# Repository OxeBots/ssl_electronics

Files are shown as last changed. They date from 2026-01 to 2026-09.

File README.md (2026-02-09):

# SSL Electronics - Oxebots

Electronics design for the RoboCup Soccer Small-Size League (SSL).

## System Architecture

*   **Main Board:** ESP32-based controller board.
*   **Power Board:** Power distribution and battery protection.
*   **Kicker Board:** Board that drives the solenoid through a capacitor bank charged up to 200V.

## Repository Structure

*   `/pcbs`: KiCad boards project files.
*   `/Libraries`: Custom symbols, footprints, and 3D models.
*   `/exported`: STEP and 3D exports.
*   `/datasheets`: Component documentation.

## Core Components

*   **Toolchain:** KiCad 9.0+
*   **MCU:** ESP32 38-pin
*   **RF:** NRF24L01+
*   **Sensors:** GY-85 (IMU), AS5600 (motor encoder), VL53L5X (ToF sensor)
*   **Motors:** BL48250 motor with driver board (for 24V).
*   **Solenoid:** 25X50TL (for 24V)

## Configuration

To resolve library dependencies in KiCad, you must configure the `OXEBOTS_SSL_LIB_DIR` path variable:

1.  Open KiCad.
2.  Go to **Preferences** > **Configure Paths...**
3.  Add a new entry (+ symbol):
    *   **Name:** `OXEBOTS_SSL_LIB_DIR`
    *   **Path:** Path to the `Libraries` folder in your local machine.

This ensures all schematic symbols, footprints, and 3D models are correctly linked.

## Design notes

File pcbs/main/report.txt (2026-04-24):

Footprints que foram alterados M3 de 'Oxebots:NRF24L01' para 'Oxebots:NRF24L01': : OK
Footprints que foram alterados M4 de 'Oxebots:NRF24L01' para 'Oxebots:NRF24L01': : OK
Footprints que foram alterados M2 de 'Oxebots:NRF24L01' para 'Oxebots:NRF24L01': : OK
Footprints que foram alterados M1 de 'Oxebots:NRF24L01' para 'Oxebots:NRF24L01': : OK
Footprints que foram alterados PCB2 de 'Oxebots:NRF24L01' para 'Oxebots:NRF24L01': : OK

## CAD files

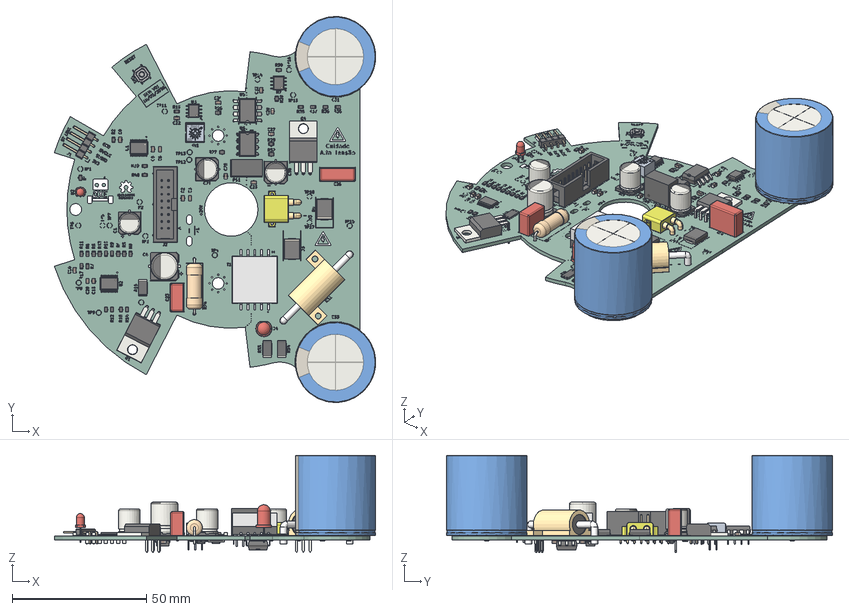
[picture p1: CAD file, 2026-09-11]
exported/kicker_board.step
119.9 x 144.0 x 36.3 mm
PinHeader_1x04_P254mm_Horizontal
CP_Elec_10x125
CP_Elec_8x10 x 3
R_0805_2012Metric x 34
C_Rect_L103mm_W50mm_P750mm_MKS4
TDK_DCT15EFD-U44S003 v1
TSSOP-20_4.4x6.5mm_P0.65mm x 2
C_0805_2012Metric x 25
TO-220-3_Horizontal_TabDown x 2
LED_D5.0mm
3362A_TAA
IDC_Header_2x08_P254mm_Vertical
DIP-8_W10.16mm
resistor_rx24_10w v1
R_Axial_DIN0617_L170mm_D60mm_P2032mm_Horizontal
R_2512_6332Metric x 4
C_Rect_L130mm_W50mm_P1000mm_FKS3_FKP3_MKS4
DIP-8_W7.62mm
LED_D3.0mm
CP_Radial_D300mm_P1000mm_SnapIn x 2
D_SMC x 2
SOIC-8_3.9x4.9mm_P1.27mm x 2
XT30PW-M
SW_SPST_SKQG_WithStem
MORNSUN BxxxxS-1WR3 v2
SOT-23 x 2
D_SMB
DIP_6_W889mm_SMDSocket
Kicker_LT3751_OxeBots_silkscreen x 2
Kicker_LT3751_OxeBots_PCB

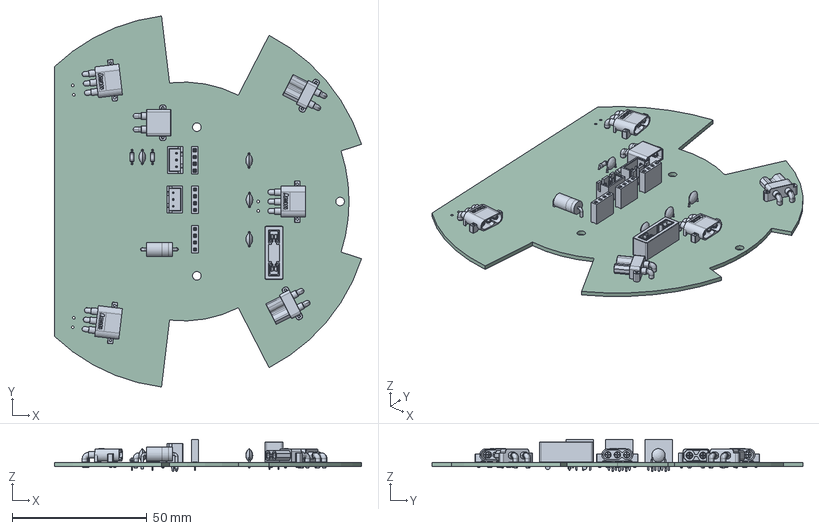
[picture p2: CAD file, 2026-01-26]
exported/power_board.step
114.0 x 137.6 x 11.9 mm
PinSocket_1x04_P2.54mm_Vertical x 3
C_Disc_D5.0mm_W2.5mm_P5.00mm x 4
power_board 1.3.1 x 3
power_board 1.3.2 x 3
power_board 1.3.3 x 3
power_board 1.3.4 x 3
power_board 1.3.5 x 3
D_DO-201_P12.70mm_Horizontal
JST_XH_B3B-XH-A_1x03_P2.50mm_Vertical x 2
XT30PW-M
R_Axial_DIN0204_L3.6mm_D1.6mm_P5.08mm_Horizontal x 2
XT30PW-F x 2
power_board_PCB

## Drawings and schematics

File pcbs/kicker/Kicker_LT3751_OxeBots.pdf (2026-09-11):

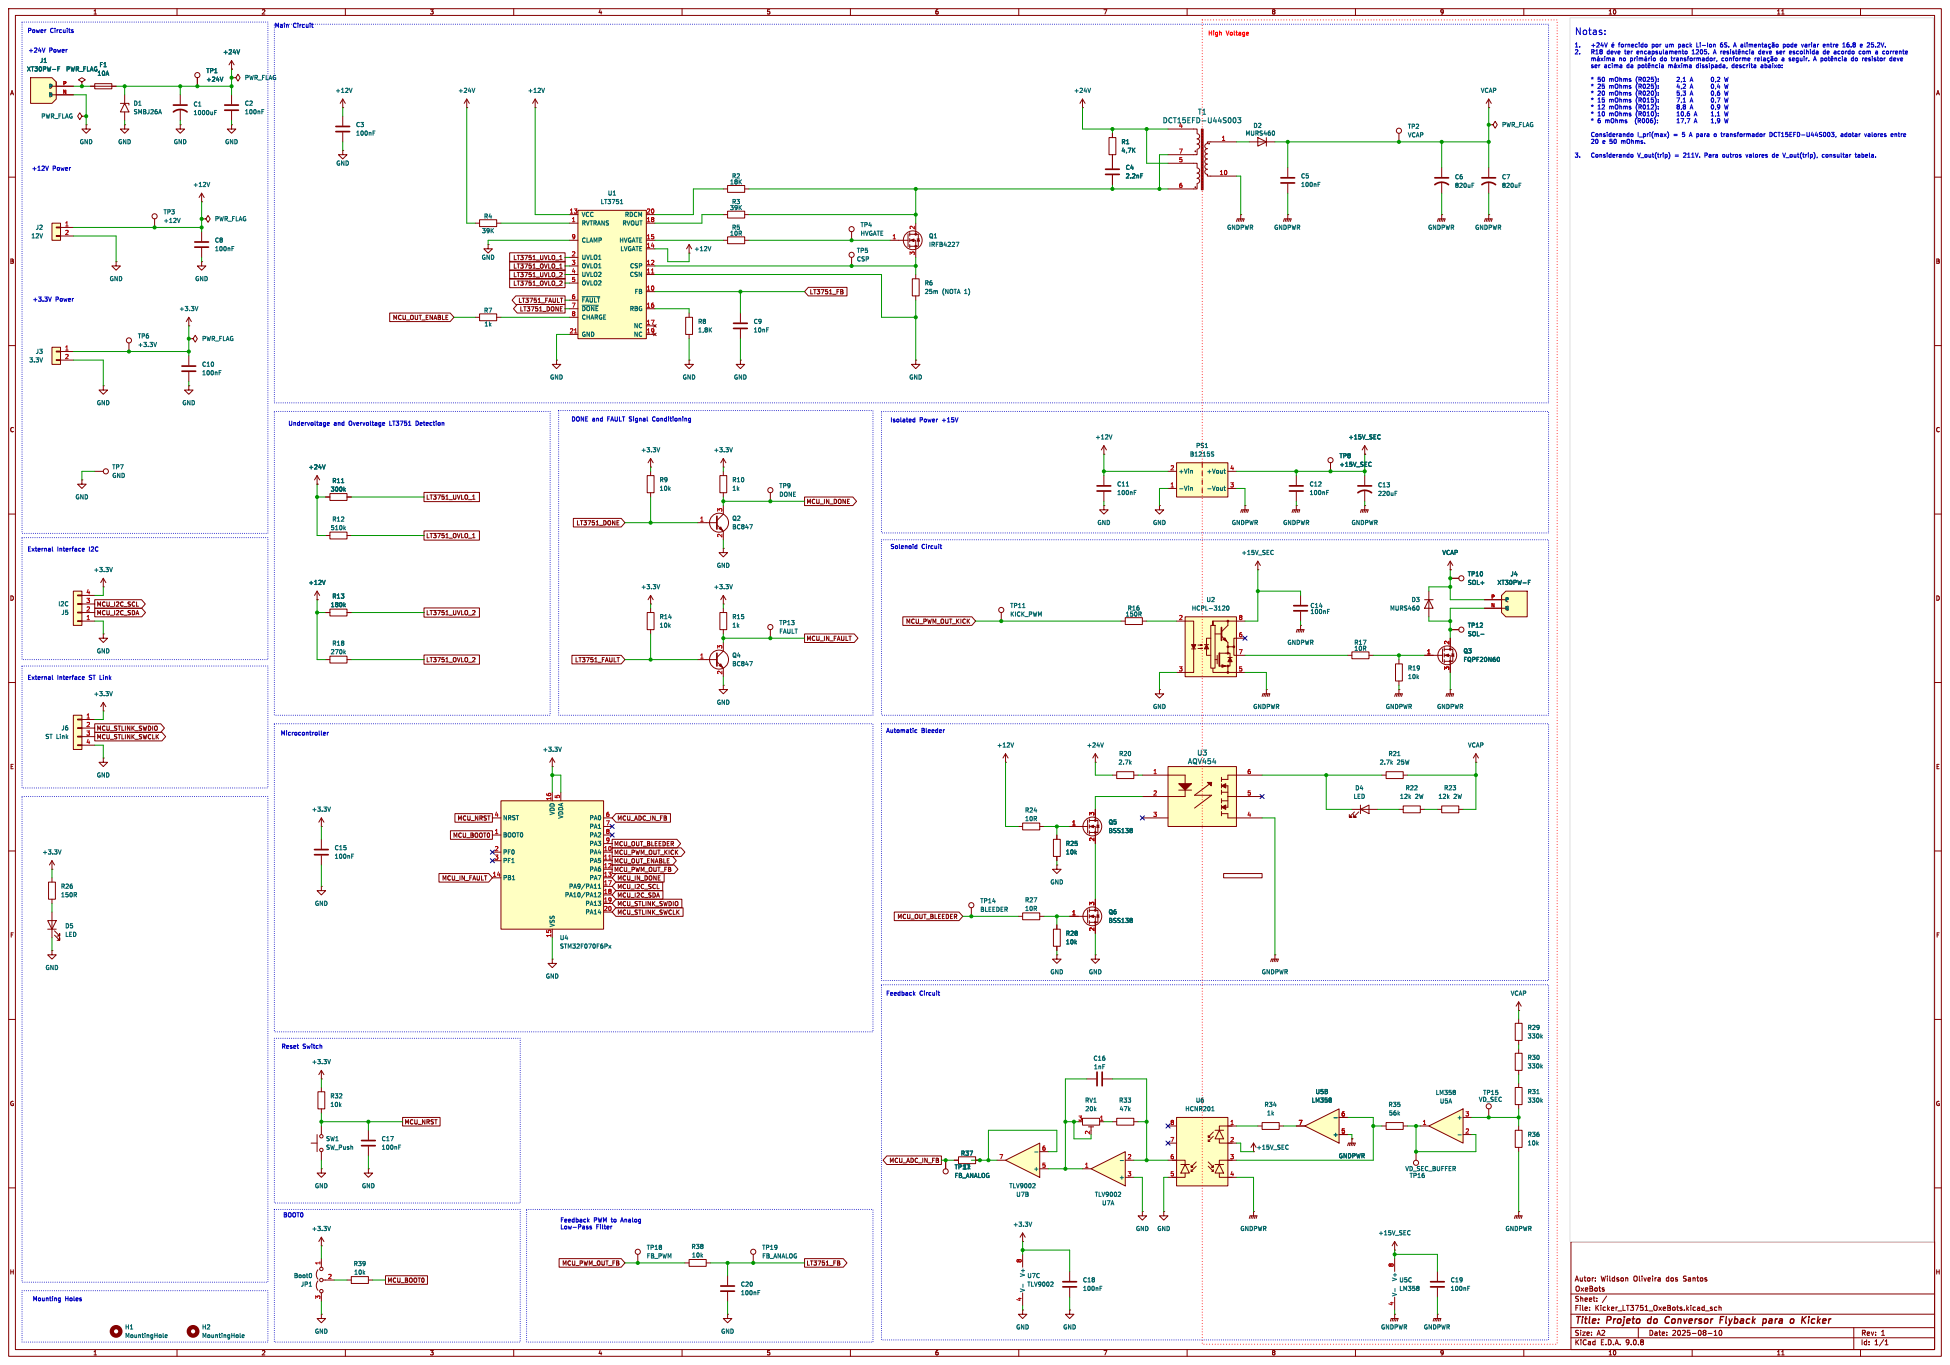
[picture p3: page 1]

LVGATE 14 CSP 12 CSN 11 FB 10 RBG 16 NC 17 NC 19 U1

Feedback PWM to Analog

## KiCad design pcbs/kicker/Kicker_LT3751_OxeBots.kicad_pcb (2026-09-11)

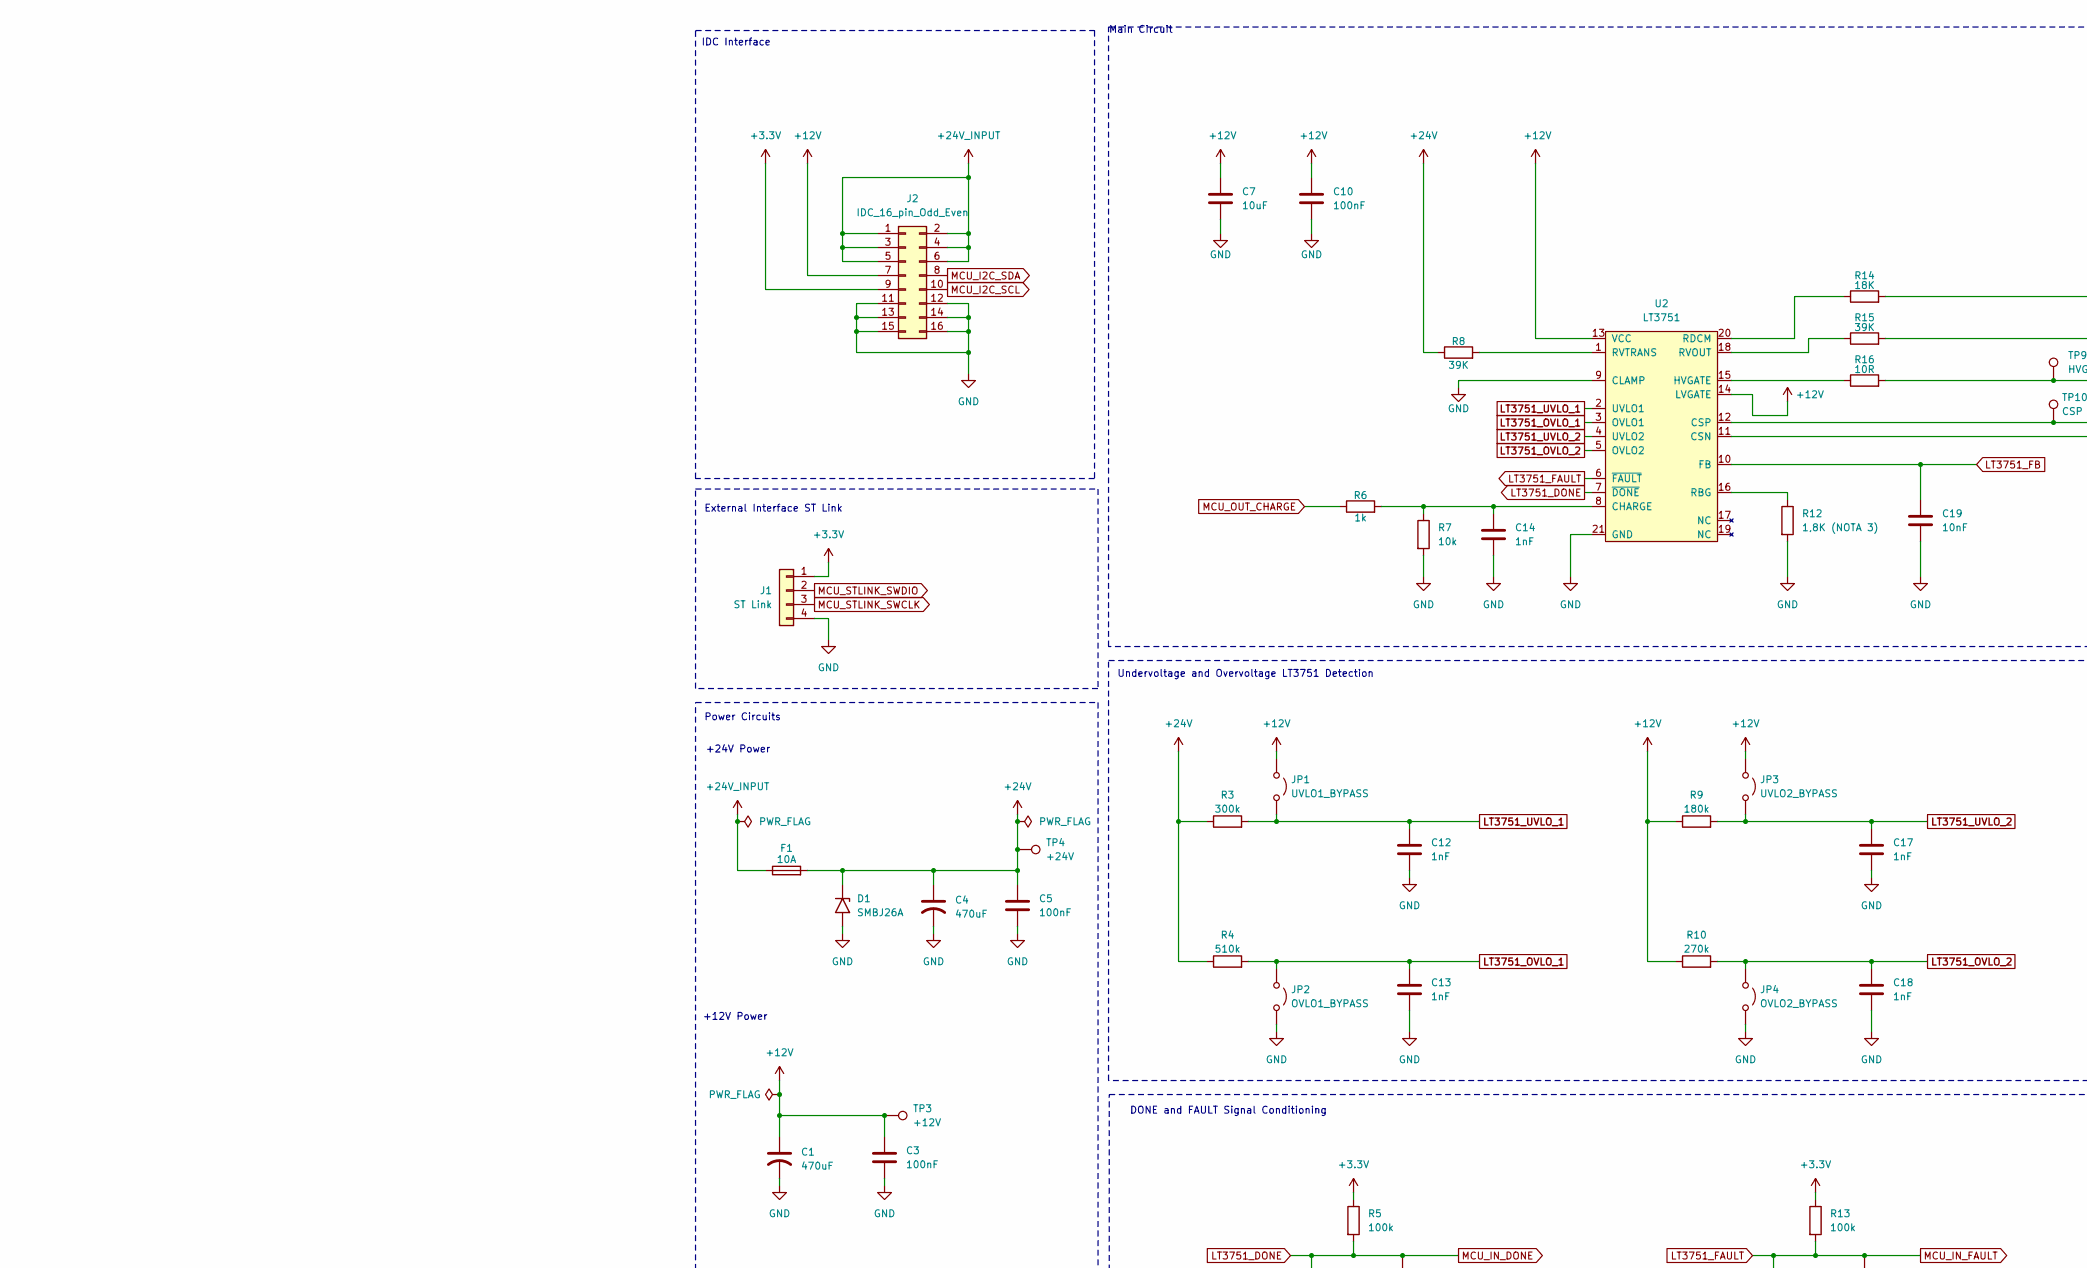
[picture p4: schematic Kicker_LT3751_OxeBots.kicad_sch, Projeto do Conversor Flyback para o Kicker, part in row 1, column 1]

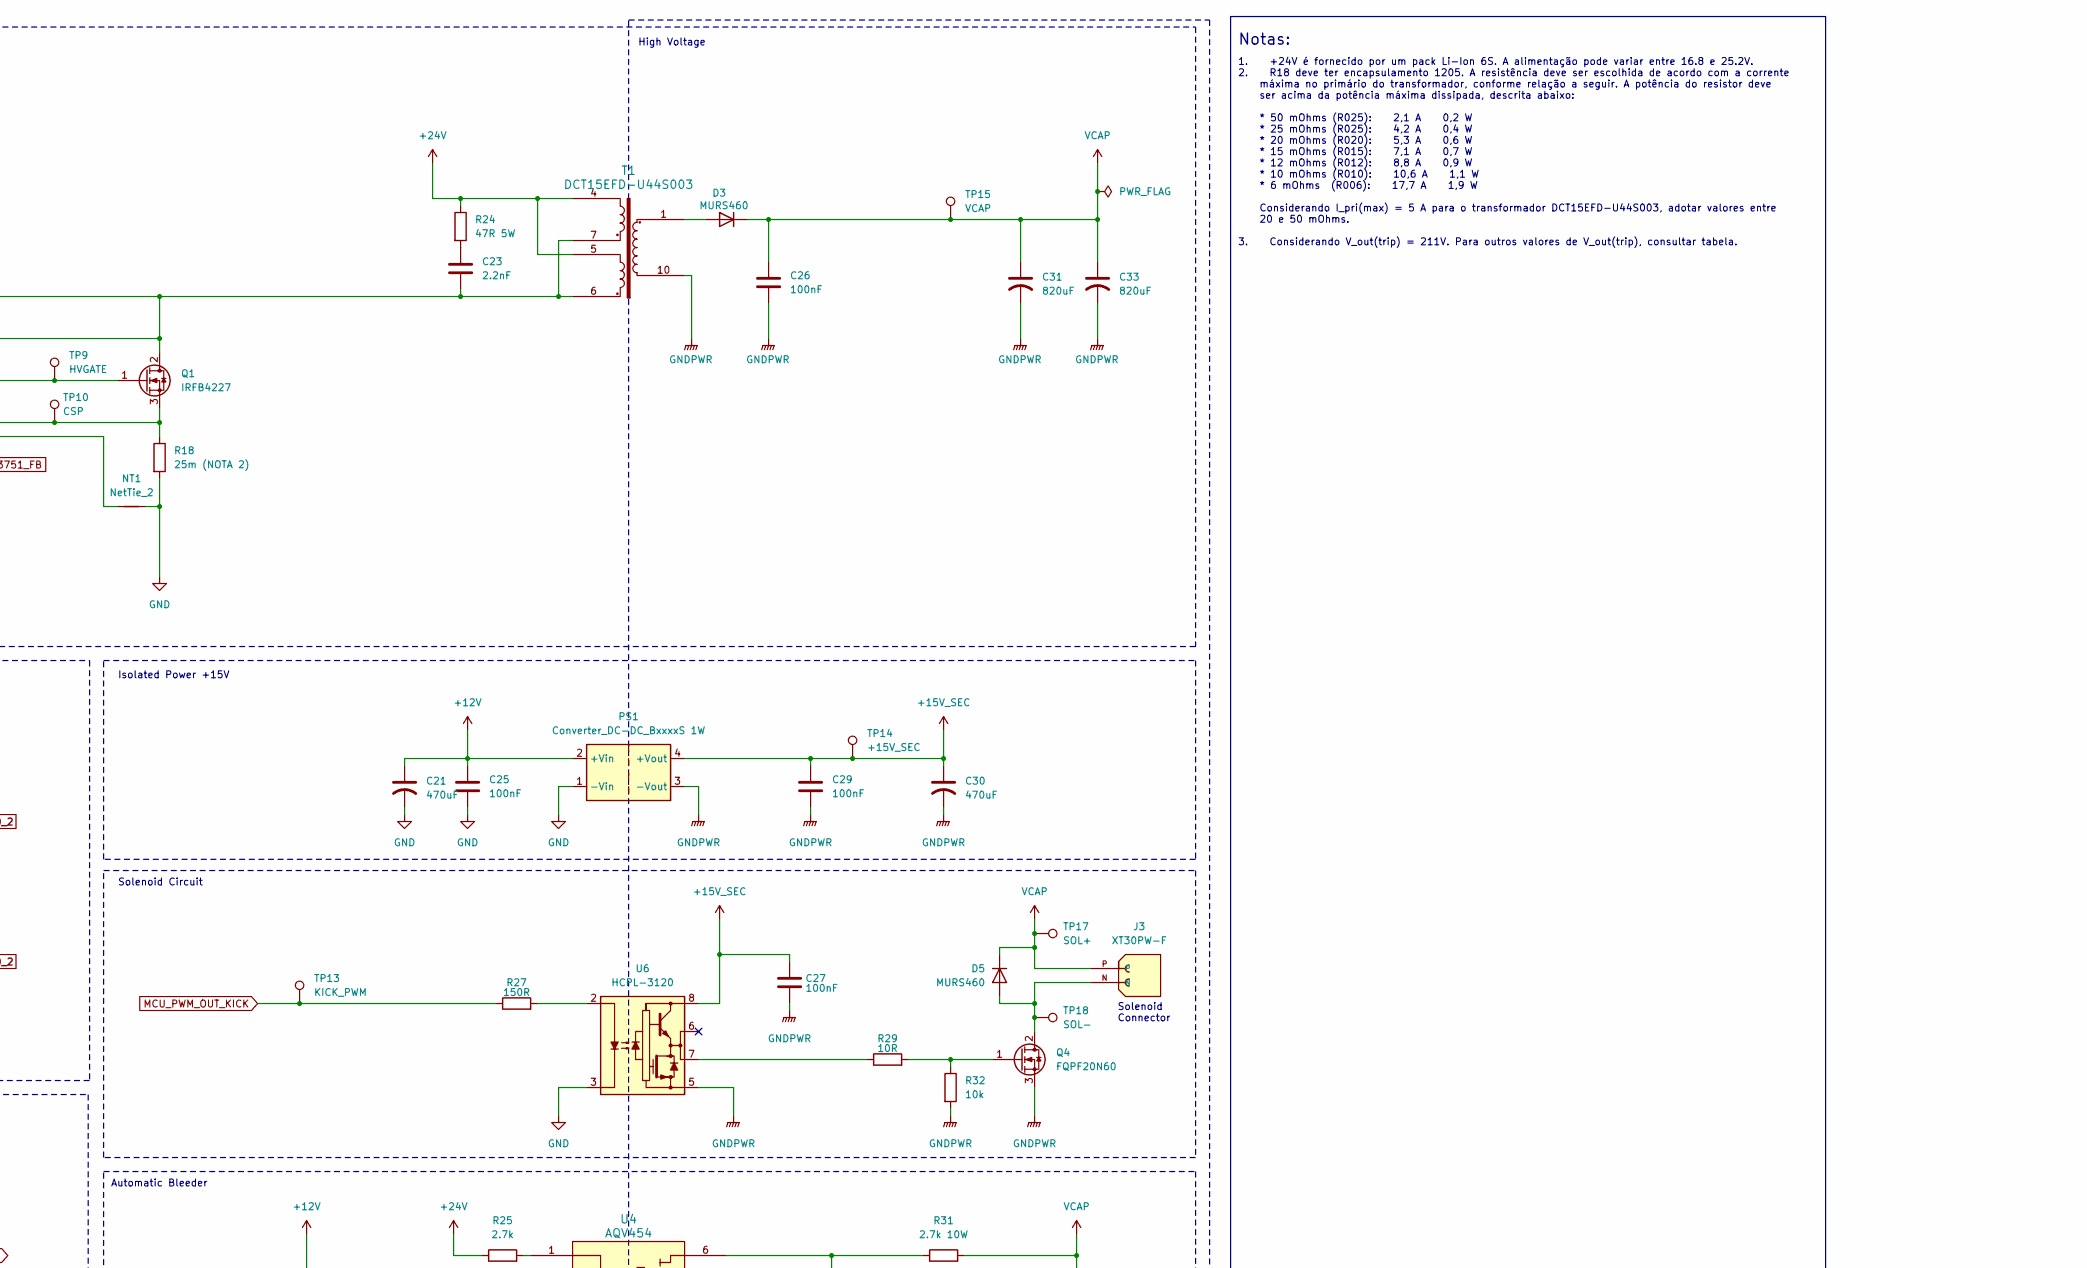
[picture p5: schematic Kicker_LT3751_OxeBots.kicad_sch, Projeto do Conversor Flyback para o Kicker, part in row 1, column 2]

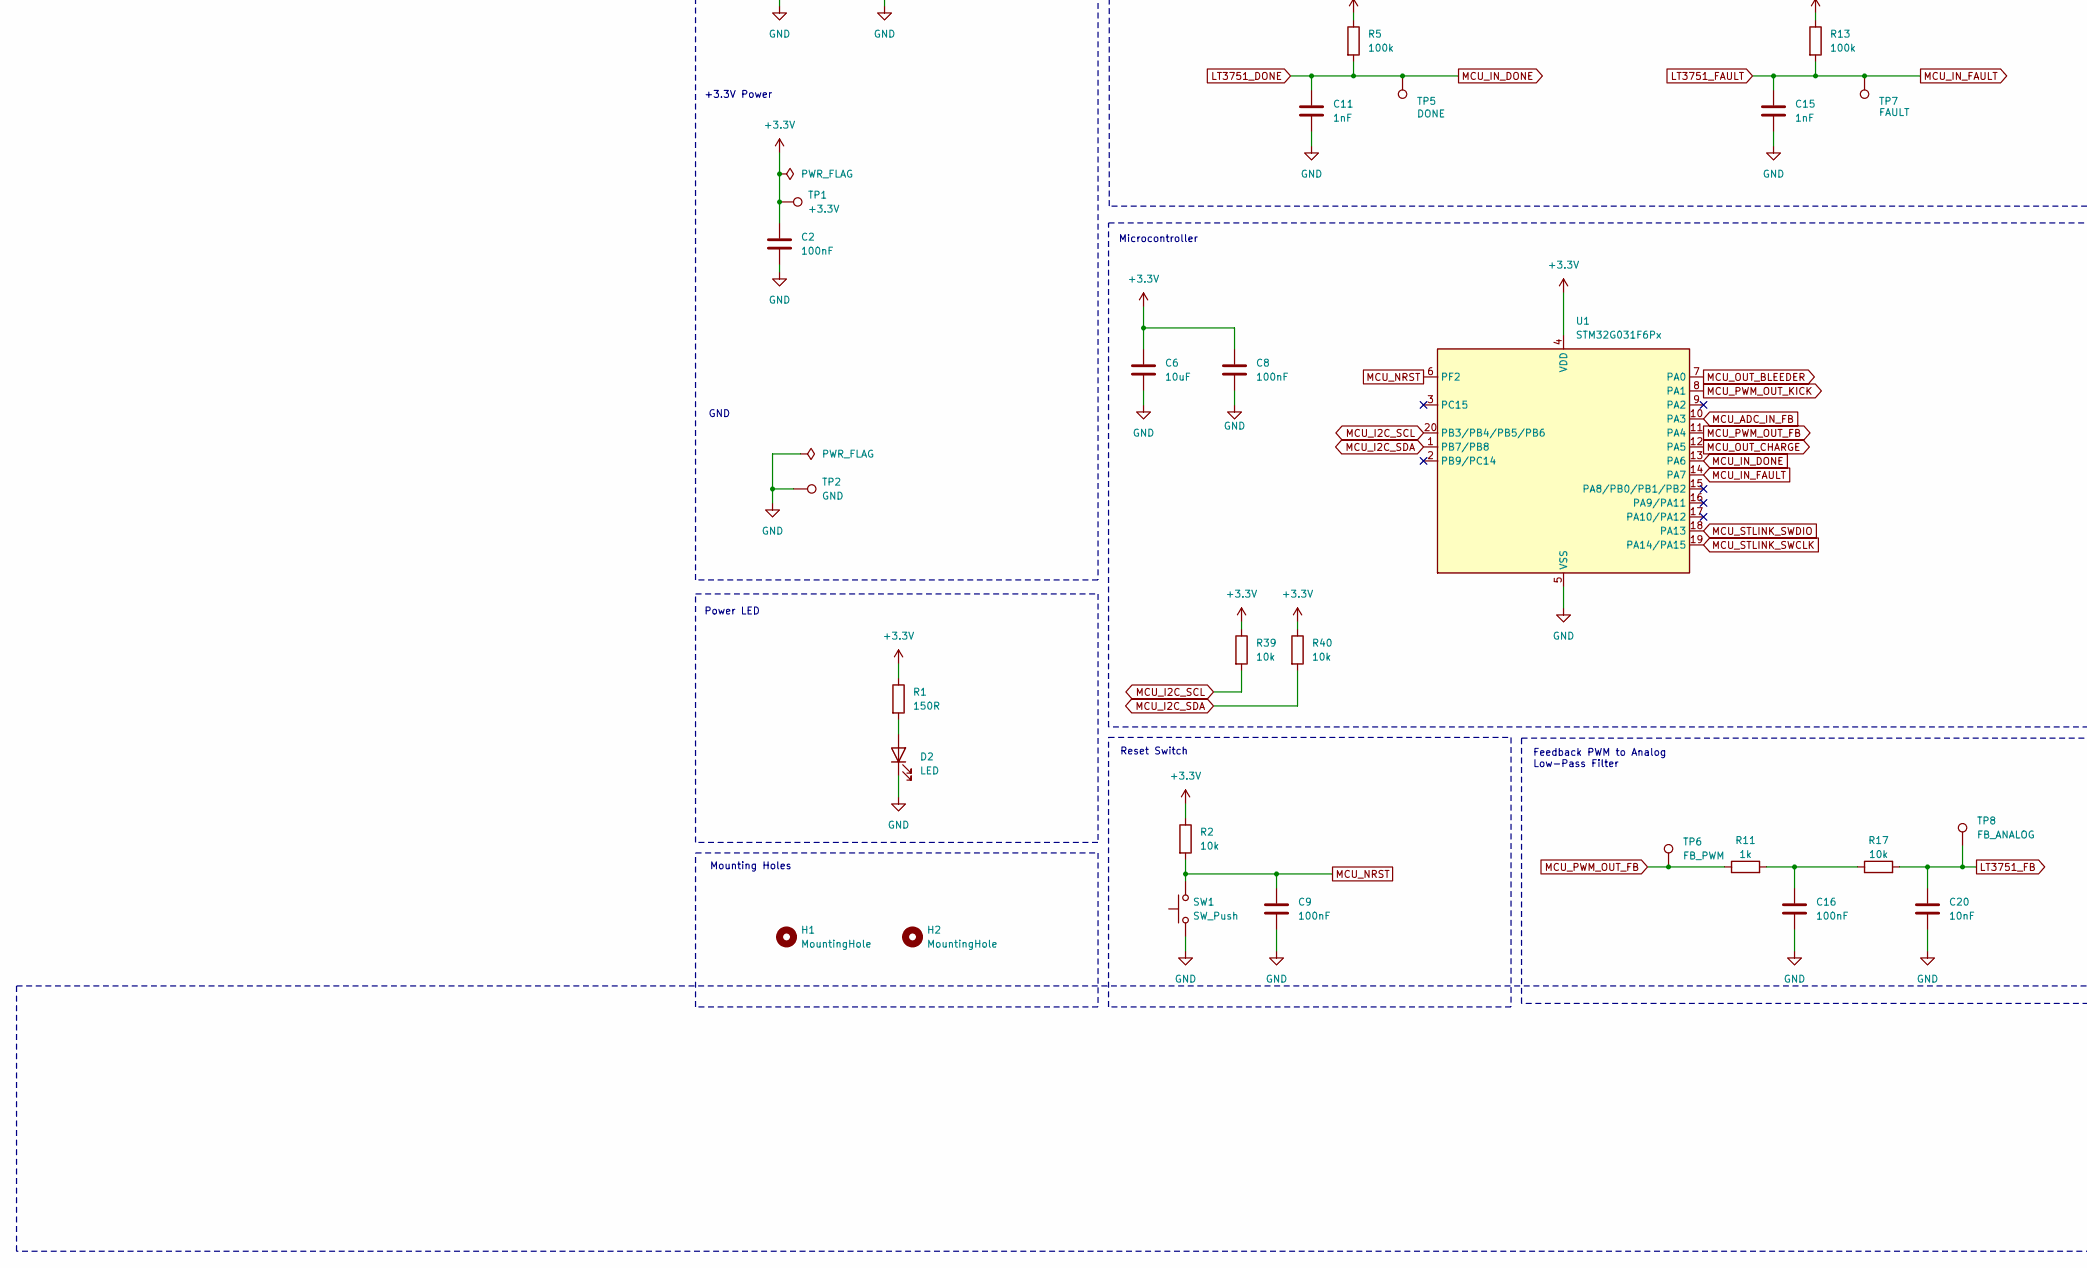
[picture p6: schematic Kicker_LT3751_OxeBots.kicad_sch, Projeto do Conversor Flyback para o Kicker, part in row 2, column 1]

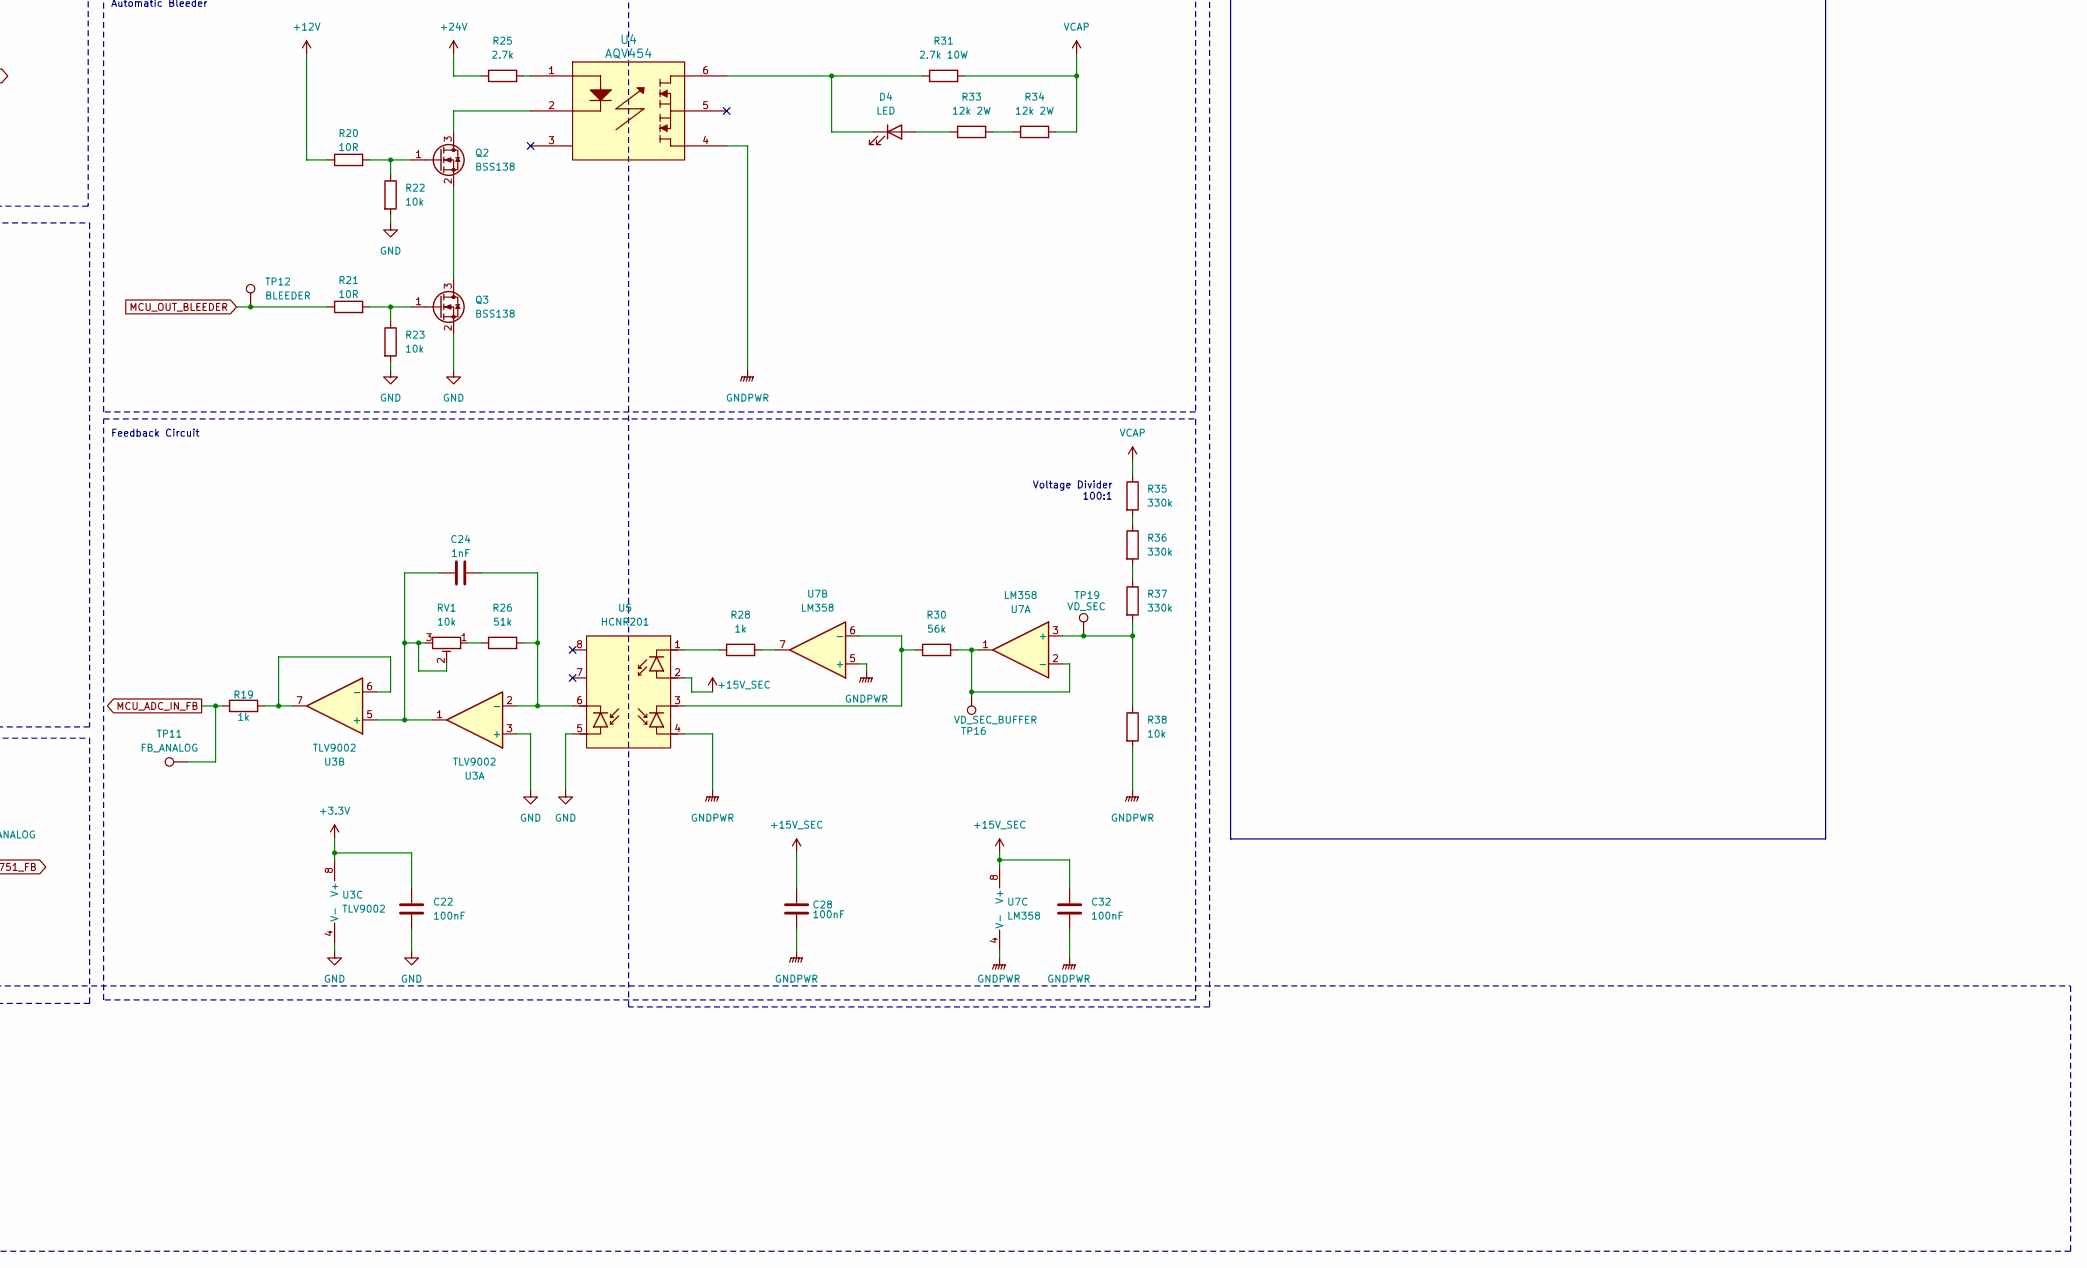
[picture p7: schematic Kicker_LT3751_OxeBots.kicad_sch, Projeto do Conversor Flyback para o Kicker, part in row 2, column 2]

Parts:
C1, C21, C30: 470uF; CP_Elec_8x10
C2, C3, C5, C8, C9, C10, C16, C22, C25, C27, C28, C29, C32: 100nF; C_0805_2012Metric_Pad1.18x1.45mm_HandSolder
C4: 470uF; CP_Elec_10x12.5
C6, C7: 10uF; C_0805_2012Metric_Pad1.18x1.45mm_HandSolder
C11, C12, C13, C14, C15, C17, C18, C24: 1nF; C_0805_2012Metric_Pad1.18x1.45mm_HandSolder
C19, C20: 10nF; C_0805_2012Metric_Pad1.18x1.45mm_HandSolder
C23: 2.2nF; C_Rect_L10.3mm_W5.0mm_P7.50mm_MKS4
C26: 100nF; C_Rect_L13.0mm_W5.0mm_P10.00mm_FKS3_FKP3_MKS4
C31, C33: 820uF; CP_Radial_D30.0mm_P10.00mm_SnapIn
D1: SMBJ26A; D_SMB
D2: LED; LED_D3.0mm
D3, D5: MURS460; D_SMC_Handsoldering
D4: LED; LED_D5.0mm
F1: 10A; Fuse_Blade_Mini_directSolder
H1, H2: MountingHole; MountingHole_4.3mm_M4_Pad_Via
J1: ST Link; PinHeader_1x04_P2.54mm_Horizontal
J2: IDC_16_pin_Odd_Even; IDC-Header_2x08_P2.54mm_Vertical
J3: XT30PW-F; AMASS_XT30PW-M; PARTREV 1.2
JP1: UVLO1_BYPASS; SolderJumper-2_P1.3mm_Open_RoundedPad1.0x1.5mm
JP2: OVLO1_BYPASS; SolderJumper-2_P1.3mm_Open_RoundedPad1.0x1.5mm
JP3: UVLO2_BYPASS; SolderJumper-2_P1.3mm_Open_RoundedPad1.0x1.5mm
JP4: OVLO2_BYPASS; SolderJumper-2_P1.3mm_Open_RoundedPad1.0x1.5mm
NT1: NetTie_2; NetTie-2_SMD_Pad0.5mm
PS1: Converter_DC-DC_BxxxxS 1W; DC-DC_Converter_BxxxxS_1W
Q1: IRFB4227; TO-220-3_Horizontal_TabDown
Q2, Q3: BSS138; SOT-23
Q4: FQPF20N60; TO-220-3_Horizontal_TabDown
R1, R27: 150R; R_0805_2012Metric_Pad1.20x1.40mm_HandSolder
R2, R7, R17, R22, R23, R32, R38, R39, R40: 10k; R_0805_2012Metric_Pad1.20x1.40mm_HandSolder
R3: 300k; R_0805_2012Metric_Pad1.20x1.40mm_HandSolder
R4: 510k; R_0805_2012Metric_Pad1.20x1.40mm_HandSolder
R5, R13: 100k; R_0805_2012Metric_Pad1.20x1.40mm_HandSolder
R6, R11, R19, R28: 1k; R_0805_2012Metric_Pad1.20x1.40mm_HandSolder
R8, R15: 39K; R_0805_2012Metric_Pad1.20x1.40mm_HandSolder
R9: 180k; R_0805_2012Metric_Pad1.20x1.40mm_HandSolder
R10: 270k; R_0805_2012Metric_Pad1.20x1.40mm_HandSolder
R12: 1,8K (NOTA 3); R_0805_2012Metric_Pad1.20x1.40mm_HandSolder
R14: 18K; R_0805_2012Metric_Pad1.20x1.40mm_HandSolder
R16, R20, R21, R29: 10R; R_0805_2012Metric_Pad1.20x1.40mm_HandSolder
R18: 25m (NOTA 2); R_2512_6332Metric
R24: 47R 5W; R_Axial_DIN0617_L17.0mm_D6.0mm_P20.32mm_Horizontal
R25: 2.7k; R_2512_6332Metric_Pad1.40x3.35mm_HandSolder
R26: 51k; R_0805_2012Metric_Pad1.20x1.40mm_HandSolder
R30: 56k; R_0805_2012Metric_Pad1.20x1.40mm_HandSolder
R31: 2.7k 10W; Resistor_RX24_10W
R33, R34: 12k 2W; R_2512_6332Metric_Pad1.40x3.35mm_HandSolder
R35, R36, R37: 330k; R_0805_2012Metric_Pad1.20x1.40mm_HandSolder
RV1: 10k; trimpot_3362P
SW1: SW_Push; SW_SPST_SKQG_WithStem
T1: DCT15EFD-U44S003; TRANS_U44S003_TDK
TP1: +3.3V; TestPoint_Pad_D1.5mm
TP2: GND; TestPoint_Pad_D1.5mm
TP3: +12V; TestPoint_Pad_D1.5mm
TP4: +24V; TestPoint_Pad_D1.5mm
TP5: DONE; TestPoint_Pad_D1.5mm
TP6: FB_PWM; TestPoint_Pad_D1.5mm
TP7: FAULT; TestPoint_Pad_D1.5mm
TP8, TP11: FB_ANALOG; TestPoint_Pad_D1.5mm
TP9: HVGATE; TestPoint_Pad_D1.5mm
TP10: CSP; TestPoint_Pad_D1.5mm
TP12: BLEEDER; TestPoint_Pad_D1.5mm
TP13: KICK_PWM; TestPoint_Pad_D1.5mm
TP14: +15V_SEC; TestPoint_Pad_D1.5mm
TP15: VCAP; TestPoint_Pad_D1.5mm
TP16: VD_SEC_BUFFER; TestPoint_Pad_D1.5mm
TP17: SOL+; TestPoint_Pad_D1.5mm
TP18: SOL-; TestPoint_Pad_D1.5mm
TP19: VD_SEC; TestPoint_Pad_D1.5mm
U1: STM32G031F6Px; TSSOP-20_4.4x6.5mm_P0.65mm
U2: LT3751; Mouser 584-LT3751EFE#PBF
U3: TLV9002; SOIC-8_3.9x4.9mm_P1.27mm
U4: AQV454
U5: HCNR201; DIP-8_W10.16mm_LongPads
U6: HCPL-3120; DIP-8_W7.62mm_LongPads
U7: LM358; SOIC-8_3.9x4.9mm_P1.27mm

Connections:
+3.3V: C2.1, C6.1, C8.1, C22.1, J1.1, J2.9, R1.1, R2.1, R5.1, R13.1, R39.1, R40.1, TP1.1 (1_1), U1.4 (VDD), U3.8 (V+)
+12V: C1.1, C3.1, C7.1, C10.1, C21.1, C25.1, J2.7, JP1.1 (A), JP3.1 (A), PS1.2 (+Vin), R9.1, R10.1, R20.1, TP3.1 (1_1), U2.13 (VCC), U2.14 (LVGATE)
+15V_SEC: C27.1, C28.1, C29.1, C30.1, C32.1, PS1.4 (+Vout), TP14.1 (1_1), U5.2, U6.8 (VCC), U7.8 (V+)
+24V: C4.1, C5.1, D1.1 (A1), F1.2, R3.1, R4.1, R8.1, R24.1, R25.1, T1.4, T1.5, TP4.1 (1_1)
+24V_INPUT: F1.1, J2.1, J2.2, J2.3, J2.4, J2.5, J2.6
GND: C1.2, C2.2, C3.2, C4.2, C5.2, C6.2, C7.2, C8.2, C9.2, C10.2, C11.2, C12.2, C13.2, C14.2, C15.2, C16.2, C17.2, C18.2, C19.2, C20.2, C21.2, C22.2, C25.2, D1.2 (A2), D2.1 (K), J1.4, J2.11, J2.12, J2.13, J2.14, J2.15, J2.16, JP2.2 (B), JP4.2 (B), NT1.2, PS1.1 (-Vin), Q3.2 (S), R7.2, R12.2, R18.2, R22.2, R23.2, SW1.1, TP2.1 (1_1), U1.5 (VSS), U2.9 (CLAMP), U2.21 (GND), U3.3 (+), U3.4 (V-), U5.5, U6.3 (C)
GNDPWR: C26.2, C27.2, C28.2, C29.2, C30.2, C31.2, C32.2, C33.2, PS1.3 (-Vout), Q4.3 (S), R32.2, R38.2, T1.10, U4.4, U5.4, U6.5 (VEE), U7.4 (V-), U7.5 (+)
LT3751_DONE: C11.1, R5.2, TP5.1 (1_1), U1.13 (PA6), U2.7 (~DONE)
LT3751_FAULT: C15.1, R13.2, TP7.1 (1_1), U1.14 (PA7), U2.6 (~FAULT)
LT3751_FB: C19.1, C20.1, R17.2, TP8.1 (1_1), U2.10 (FB)
LT3751_OVLO_1: C13.1, JP2.1 (A), R4.2, U2.3 (OVLO1)
LT3751_OVLO_2: C18.1, JP4.1 (A), R10.2, U2.5 (OVLO2)
LT3751_UVLO_1: C12.1, JP1.2 (B), R3.2, U2.2 (UVLO1)
LT3751_UVLO_2: C17.1, JP3.2 (B), R9.2, U2.4 (UVLO2)
MCU_ADC_IN_FB: R19.1, TP11.1 (1_1), U1.10 (PA3)
MCU_I2C_SCL: J2.10, R39.2, U1.20 (PB3/PB4/PB5/PB6)
MCU_I2C_SDA: J2.8, R40.2, U1.1 (PB7/PB8)
MCU_NRST: C9.1, R2.2, SW1.2, U1.6 (PF2)
MCU_OUT_BLEEDER: R21.1, TP12.1 (1_1), U1.7 (PA0)
MCU_OUT_CHARGE: R6.1, U1.12 (PA5)
MCU_PWM_OUT_FB: R11.1, TP6.1 (1_1), U1.11 (PA4)
MCU_PWM_OUT_KICK: R27.1, TP13.1 (1_1), U1.8 (PA1)
MCU_STLINK_SWCLK: J1.3, U1.19 (PA14/PA15)
MCU_STLINK_SWDIO: J1.2, U1.18 (PA13)
unnamed: C16.1, R11.2, R17.1
unnamed: C23.1, R24.2
unnamed: D2.2 (A), R1.2
unnamed: D3.2 (A), T1.1
unnamed: D4.2 (A), R33.1
unnamed: D4.1 (K), R31.1, U4.6
unnamed: D5.2 (A), J3.N, Q4.2 (D), TP18.1 (1_1)
unnamed: C23.2, Q1.2 (D), R14.2, R15.2, T1.6, T1.7
unnamed: Q1.1 (G), R16.2, TP9.1 (1_1)
unnamed: Q1.3 (S), R18.1, TP10.1 (1_1), U2.12 (CSP)
unnamed: Q2.3 (D), U4.2
unnamed: Q2.1 (G), R20.2, R22.1
unnamed: Q2.2 (S), Q3.3 (D)
unnamed: Q3.1 (G), R21.2, R23.1
unnamed: Q4.1 (G), R29.2, R32.1
unnamed: R25.2, U4.1
unnamed: R26.1, RV1.1
unnamed: R28.1, U5.1
unnamed: R28.2, U7.7
unnamed: R29.1, U6.7 (VO)
unnamed: R33.2, R34.1
unnamed: R35.2, R36.1
unnamed: R36.2, R37.1
unnamed: C14.1, R6.2, R7.1, U2.8 (CHARGE)
unnamed: NT1.1, U2.11 (CSN)
unnamed: R16.1, U2.15 (HVGATE)
unnamed: R12.1, U2.16 (RBG)
unnamed: R14.1, U2.20 (RDCM)
unnamed: R15.1, U2.18 (RVOUT)
unnamed: R8.2, U2.1 (RVTRANS)
unnamed: C24.1, R26.2, U3.2 (-), U5.6
unnamed: C24.2, RV1.2, RV1.3, U3.1, U3.5 (+)
unnamed: R19.2, U3.6 (-), U3.7
unnamed: R27.2, U6.2 (A)
unnamed: R37.2, R38.1, TP19.1 (1_1), U7.3 (+)
unnamed: R30.2, TP16.1 (1_1), U7.1, U7.2 (-)
unnamed: R30.1, U5.3, U7.6 (-)
VCAP: C26.1, C31.1, C33.1, D3.1 (K), D5.1 (K), J3.P, R31.2, R34.2, R35.1, TP15.1 (1_1), TP17.1 (1_1)

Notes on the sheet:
Power Circuits
High Voltage
Isolated Power +15V
IDC Interface
Notas:
Automatic Bleeder
Power LED
Feedback Circuit
Microcontroller
+24V Power
DONE and FAULT Signal Conditioning
Main Circuit
Voltage Divider 100:1
Solenoid Circuit
+12V Power
Mounting Holes
+3.3V Power
Reset Switch
GND
1. +24V é fornecido por um pack Li-Ion 6S. A alimentação pode variar entre 16.8 e 25.2V. 2. R18 deve ter encapsulamento 1205. A resistência deve ser escolhida de acordo com a corrente máxima no primário do transformador, conforme relação a seguir. A potência do resistor deve ser acima da potência m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
Solenoid Connector
Feedback PWM to Analog Low-Pass Filter
Undervoltage and Overvoltage LT3751 Detection
External Interface ST Link

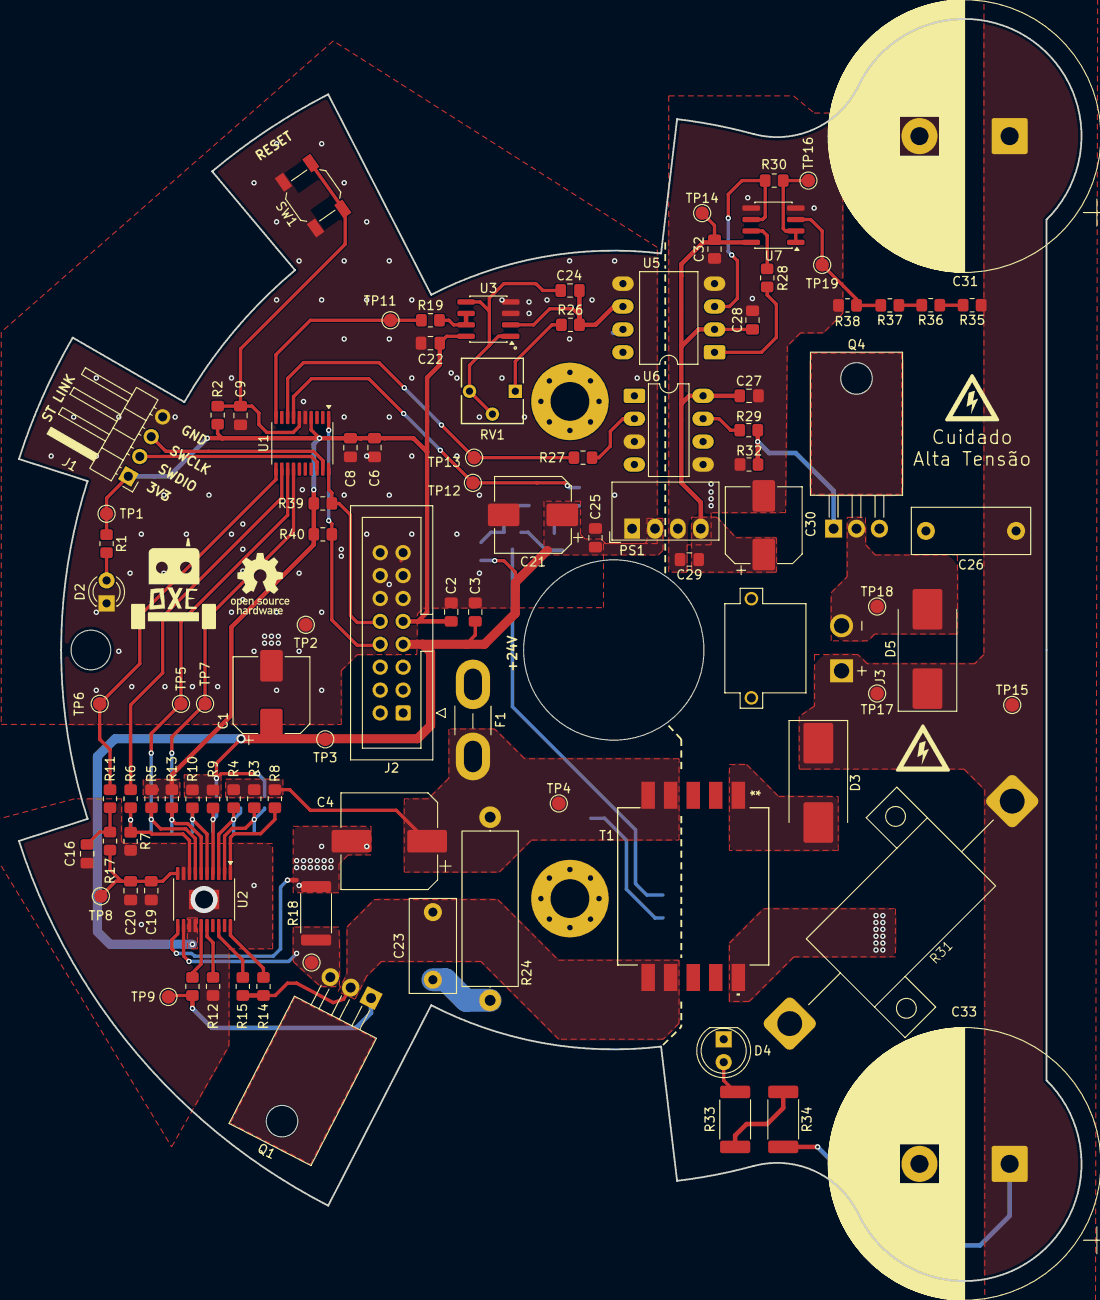
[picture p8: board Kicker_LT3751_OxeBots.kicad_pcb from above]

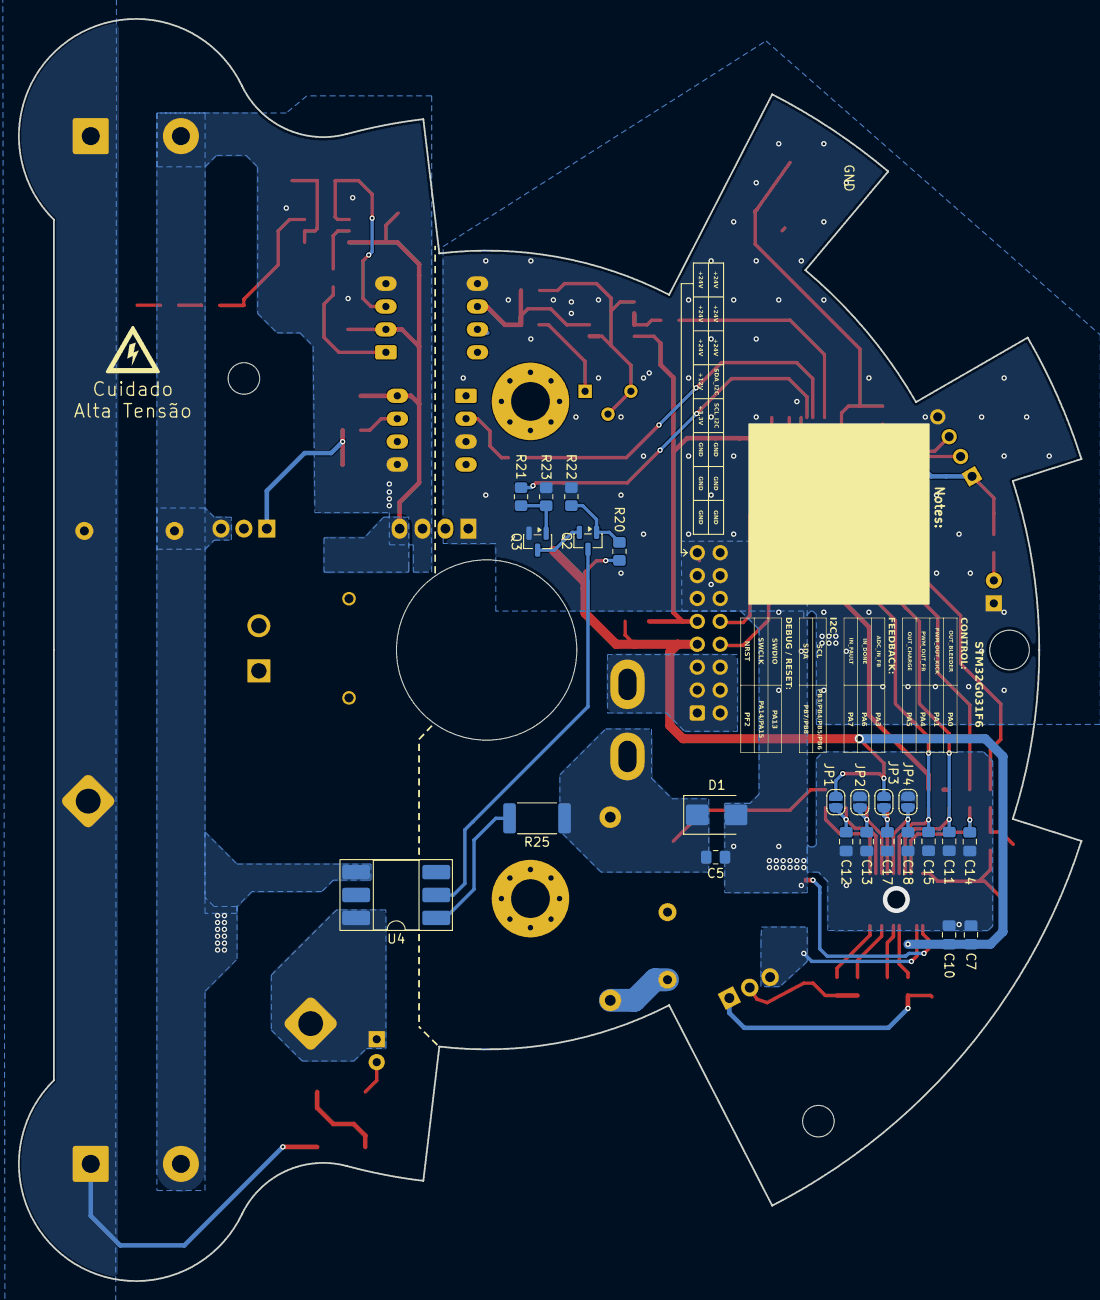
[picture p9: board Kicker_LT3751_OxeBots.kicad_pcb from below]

Board: 2 copper layers, 117.9 x 140.0 mm, 123 parts (23 on the bottom side), 62 nets.

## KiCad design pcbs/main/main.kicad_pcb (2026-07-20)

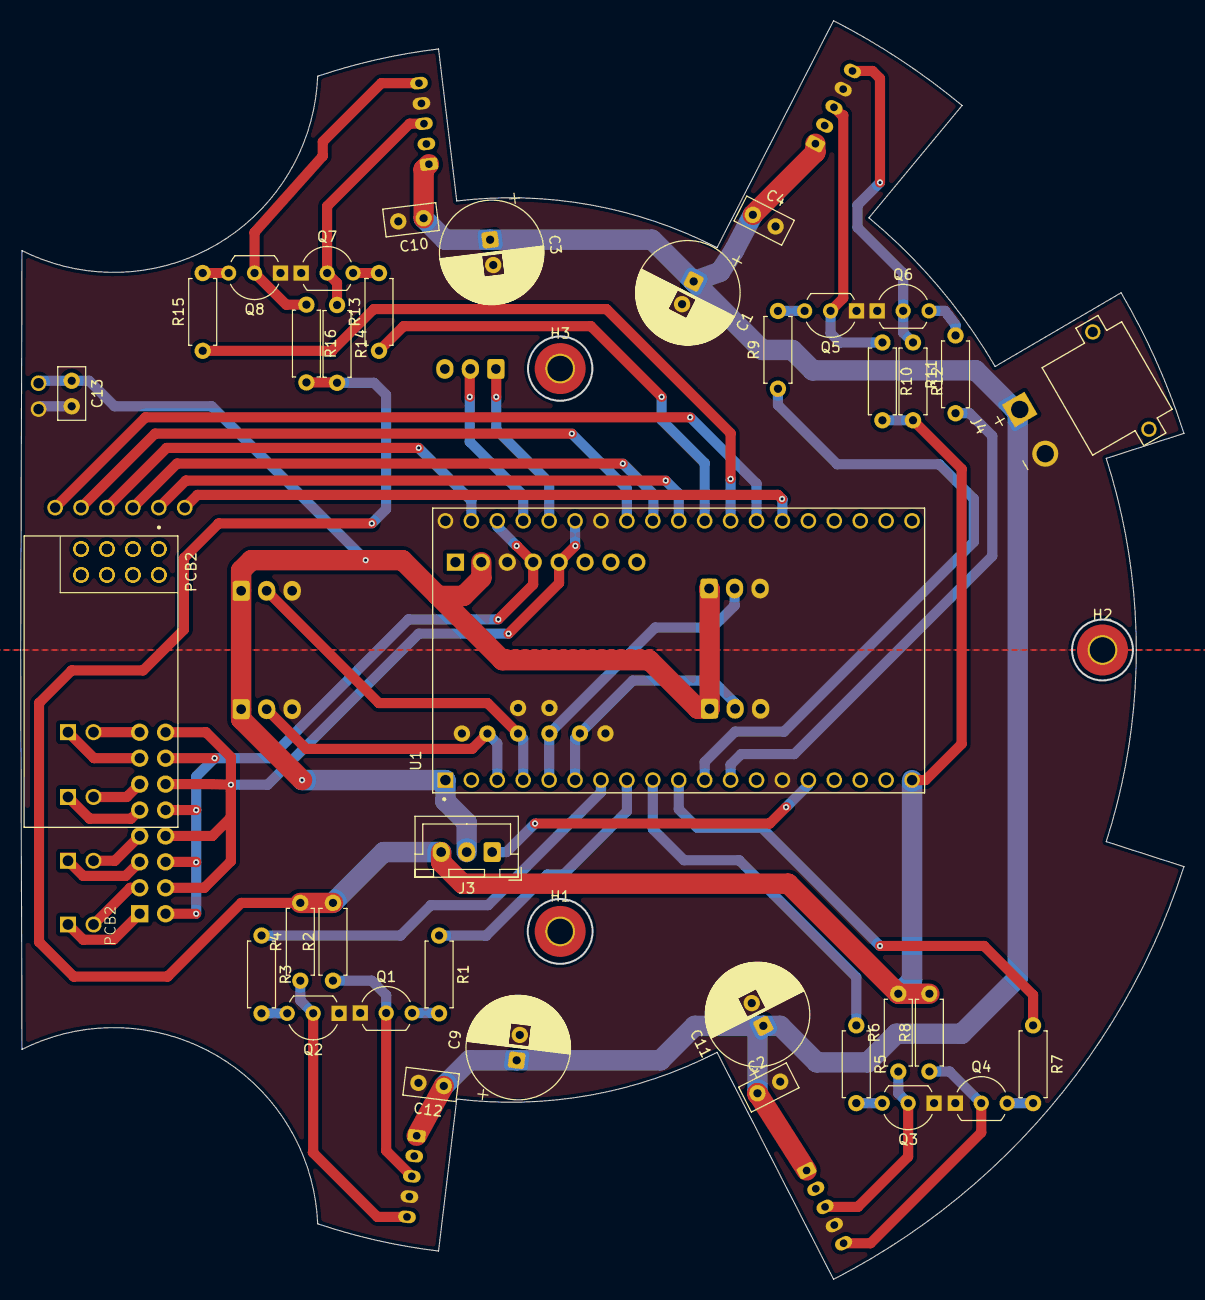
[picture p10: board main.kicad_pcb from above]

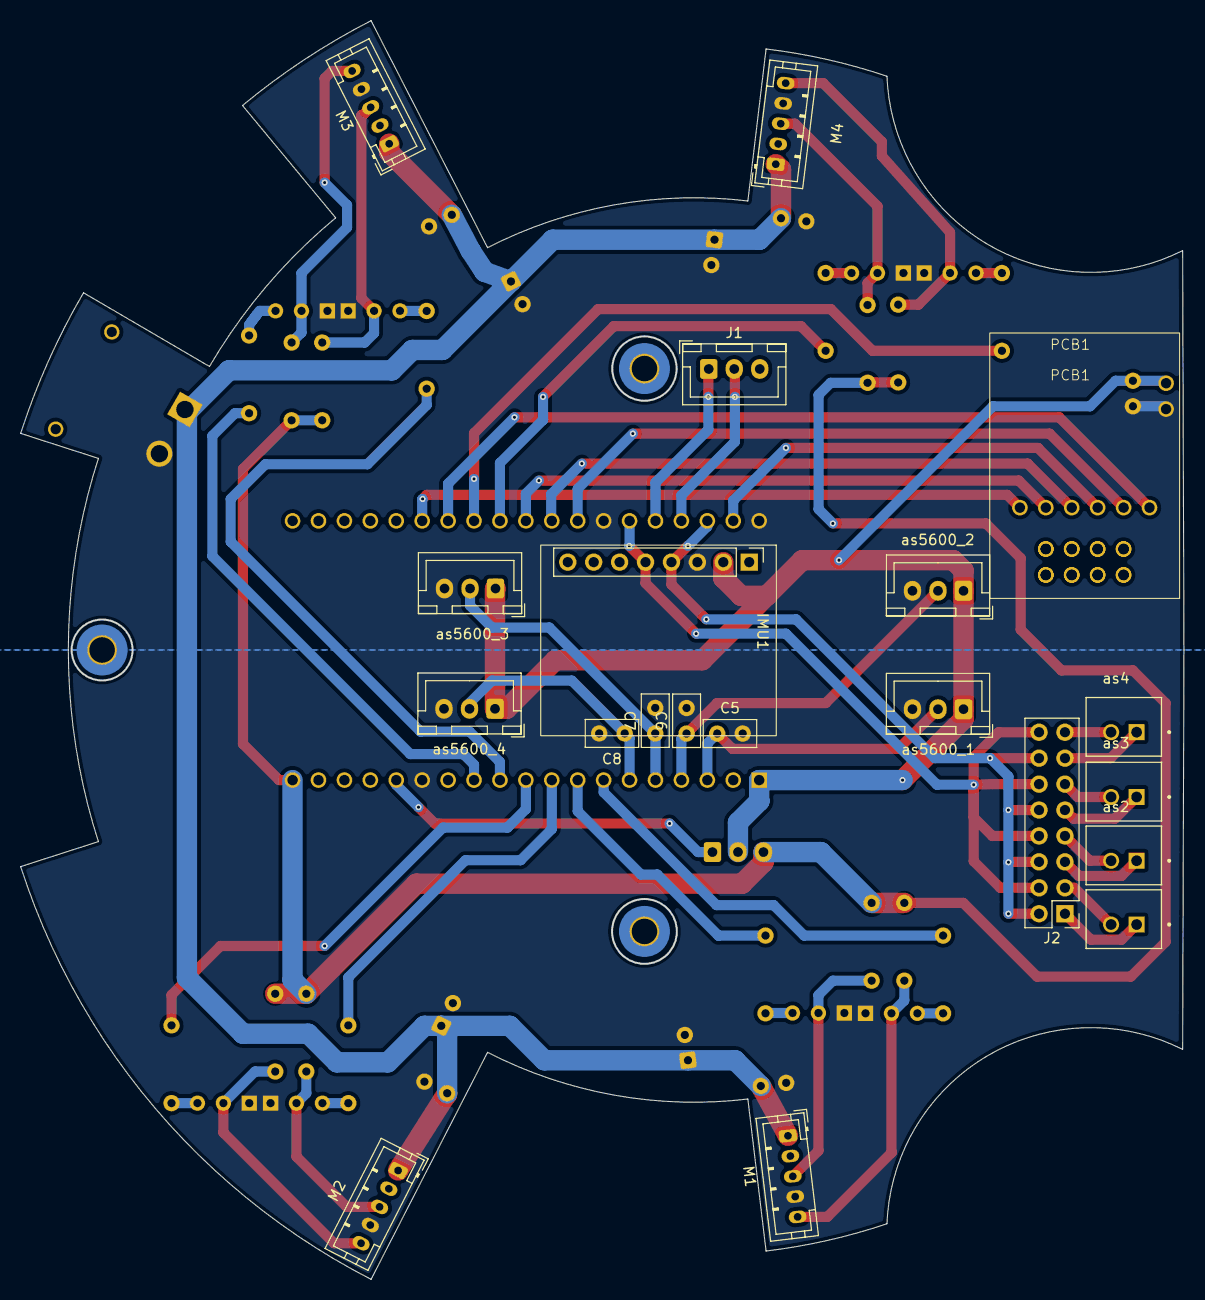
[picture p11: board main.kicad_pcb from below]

Board: 2 copper layers, 114.0 x 123.3 mm, 60 parts (20 on the bottom side), 59 nets.

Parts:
C1, C3, C9, C11: 47uF; CP_Radial_D10.0mm_P2.50mm
C2, C4, C5, C6, C7, C8, C10, C12, C13: 100 nF; C_Disc_D5.0mm_W2.5mm_P2.50mm
H1, H2, H3: MountingHole; MountingHole_2.5mm_Pad_TopBottom
IMU1: GY 85; GY-085
J1, J3: JST_XH_B3B; JST_XH_B3B-XH-A_1x03_P2.50mm_Vertical
J2: Jumpers; PinHeader_2x08_P2.54mm_Vertical
J4: XT30PW-M; AMASS_XT30PW-M
M1, M2, M3, M4: HY-5_P2.00mm_Vertical
PCB1: NRF24L01_PWR_ADP
PCB2: NRF24L01
Q1, Q2, Q3, Q4, Q5, Q6, Q7, Q8: 2SC945; TO-92L_Inline_Wide
R1, R2, R3, R4, R5, R6, R7, R8, R9, R10, R11, R12, R13, R14, R15, R16: 10k; R_Axial_DIN0207_L6.3mm_D2.5mm_P7.62mm_Horizontal
U1: ESP32-DEVKITC-32U; MODULE_ESP32-DEVKITC-32U
as1: M1_ENC_I2C; JST_B2B-XH-A
as2: M2_ENC_I2C; JST_B2B-XH-A
as3: M3_ENC_I2C; JST_B2B-XH-A
as4: M4_ENC_I2C; JST_B2B-XH-A
as5600_1: M1_ENC_AN; JST_XH_B3B-XH-A_1x03_P2.50mm_Vertical
as5600_2: M2_ENC_AN; JST_XH_B3B-XH-A_1x03_P2.50mm_Vertical
as5600_3: M3_ENC_AN; JST_XH_B3B-XH-A_1x03_P2.50mm_Vertical
as5600_4: M4_ENC_AN; JST_XH_B3B-XH-A_1x03_P2.50mm_Vertical

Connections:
+3.3V: C13.1, IMU1.2, J3.2, PCB1.15 (VCC), U1.1 (3V3), as5600_1.1, as5600_2.1, as5600_3.1, as5600_4.1
+5V: J3.3, R2.2, R4.2, R6.2, R8.2, R10.2, R12.2, R14.2, R16.2, U1.19 (EXT_5V)
+24V: C1.1, C2.1, C3.1, C4.1, C9.1, C10.1, C11.1, C12.1, J4.P, M1.1 (VCC), M2.1 (VCC), M3.1 (VCC), M4.1 (VCC)
/esp32/I2C.SCL: IMU1.4, J2.2, J2.6, J2.10, J2.14, U1.36 (IO22)
/esp32/I2C.SDA: IMU1.5, J2.4, J2.8, J2.12, J2.16, U1.33 (IO21)
/esp32/KICKER_EN: J1.1, U1.34 (RXD0)
/esp32/KICKER_PWM: J1.2, U1.35 (TXD0)
/esp32/M1_DIR: R1.1, U1.8 (IO33)
/esp32/M1_ENC: C5.1, U1.3 (SENSOR_VP), as5600_1.2
/esp32/M1_PWM: R3.1, U1.7 (IO32)
/esp32/M2_DIR: R5.1, U1.9 (IO25)
/esp32/M2_ENC: C6.1, U1.4 (SENSOR_VN), as5600_2.2
/esp32/M2_PWM: R7.1, U1.10 (IO26)
/esp32/M3_DIR: R9.1, U1.11 (IO27)
/esp32/M3_ENC: C7.1, U1.5 (IO34), as5600_3.2
/esp32/M3_PWM: R11.1, U1.12 (IO14)
/esp32/M4_DIR: R13.1, U1.28 (IO17)
/esp32/M4_ENC: C8.1, U1.6 (IO35), as5600_4.2
/esp32/M4_PWM: R15.1, U1.27 (IO16)
/esp32/RADIO.CE: PCB1.9 (CE_{mcu}), U1.25 (IO0)
/esp32/RADIO.CLK: PCB1.11 (SCK_{mcu}), U1.30 (IO18)
/esp32/RADIO.CS: PCB1.10 (CSN_{mcu}), U1.29 (IO5)
/esp32/RADIO.IRQ: PCB1.14 (IRQ_{mcu}), U1.26 (IO4)
/esp32/RADIO.MISO: PCB1.13 (MISO_{mcu}), U1.31 (IO19)
/esp32/RADIO.MOSI: PCB1.12 (MOSI_{mcu}), U1.37 (IO23)
/esp32/V_{MON}: J3.1, U1.15 (IO13)
GND: C1.2, C2.2, C3.2, C4.2, C5.2, C6.2, C7.2, C8.2, C9.2, C10.2, C11.2, C12.2, C13.2, IMU1.3, J4.N, M1.4 (GND), M2.4 (GND), M3.4 (GND), M4.4 (GND), PCB1.16 (GND), Q1.1 (E), Q2.1 (E), Q3.1 (E), Q4.1 (E), Q5.1 (E), Q6.1 (E), Q7.1 (E), Q8.1 (E), U1.14 (GND1), U1.32 (GND2), U1.38 (GND3), as5600_1.3, as5600_2.3, as5600_3.3, as5600_4.3
unnamed: J2.1, as1.1
unnamed: J2.3, as1.2
unnamed: J2.5, as2.1
unnamed: J2.7, as2.2
unnamed: J2.9, as3.1
unnamed: J2.11, as3.2
unnamed: J2.13, as4.1
unnamed: J2.15, as4.2
unnamed: M1.3 (DIR), Q1.2 (C), R2.1
unnamed: M1.5 (PWM), Q2.2 (C), R4.1
unnamed: M2.3 (DIR), Q3.2 (C), R6.1
unnamed: M2.5 (PWM), Q4.2 (C), R8.1
unnamed: M3.3 (DIR), Q5.2 (C), R10.1
unnamed: M3.5 (PWM), Q6.2 (C), R12.1
unnamed: M4.3 (DIR), Q7.2 (C), R14.1
unnamed: M4.5 (PWM), Q8.2 (C), R16.1
unnamed: PCB1.2 (CE), PCB2.2 (CE)
unnamed: PCB1.6 (CSN), PCB2.6 (CSN)
unnamed: PCB1.1 (GND_{out}), PCB2.1 (GND_{out})
unnamed: PCB1.8 (IRQ), PCB2.8 (IRQ)
unnamed: PCB1.4 (MISO), PCB2.4 (MISO)
unnamed: PCB1.7 (MOSI), PCB2.7 (MOSI)
unnamed: PCB1.3 (SCK), PCB2.3 (SCK)
unnamed: PCB1.5 (VCC_{out}), PCB2.5 (VCC_{out})
unnamed: Q1.3 (B), R1.2
unnamed: Q2.3 (B), R3.2
unnamed: Q3.3 (B), R5.2
unnamed: Q4.3 (B), R7.2
unnamed: Q5.3 (B), R9.2
unnamed: Q6.3 (B), R11.2
unnamed: Q7.3 (B), R13.2
unnamed: Q8.3 (B), R15.2

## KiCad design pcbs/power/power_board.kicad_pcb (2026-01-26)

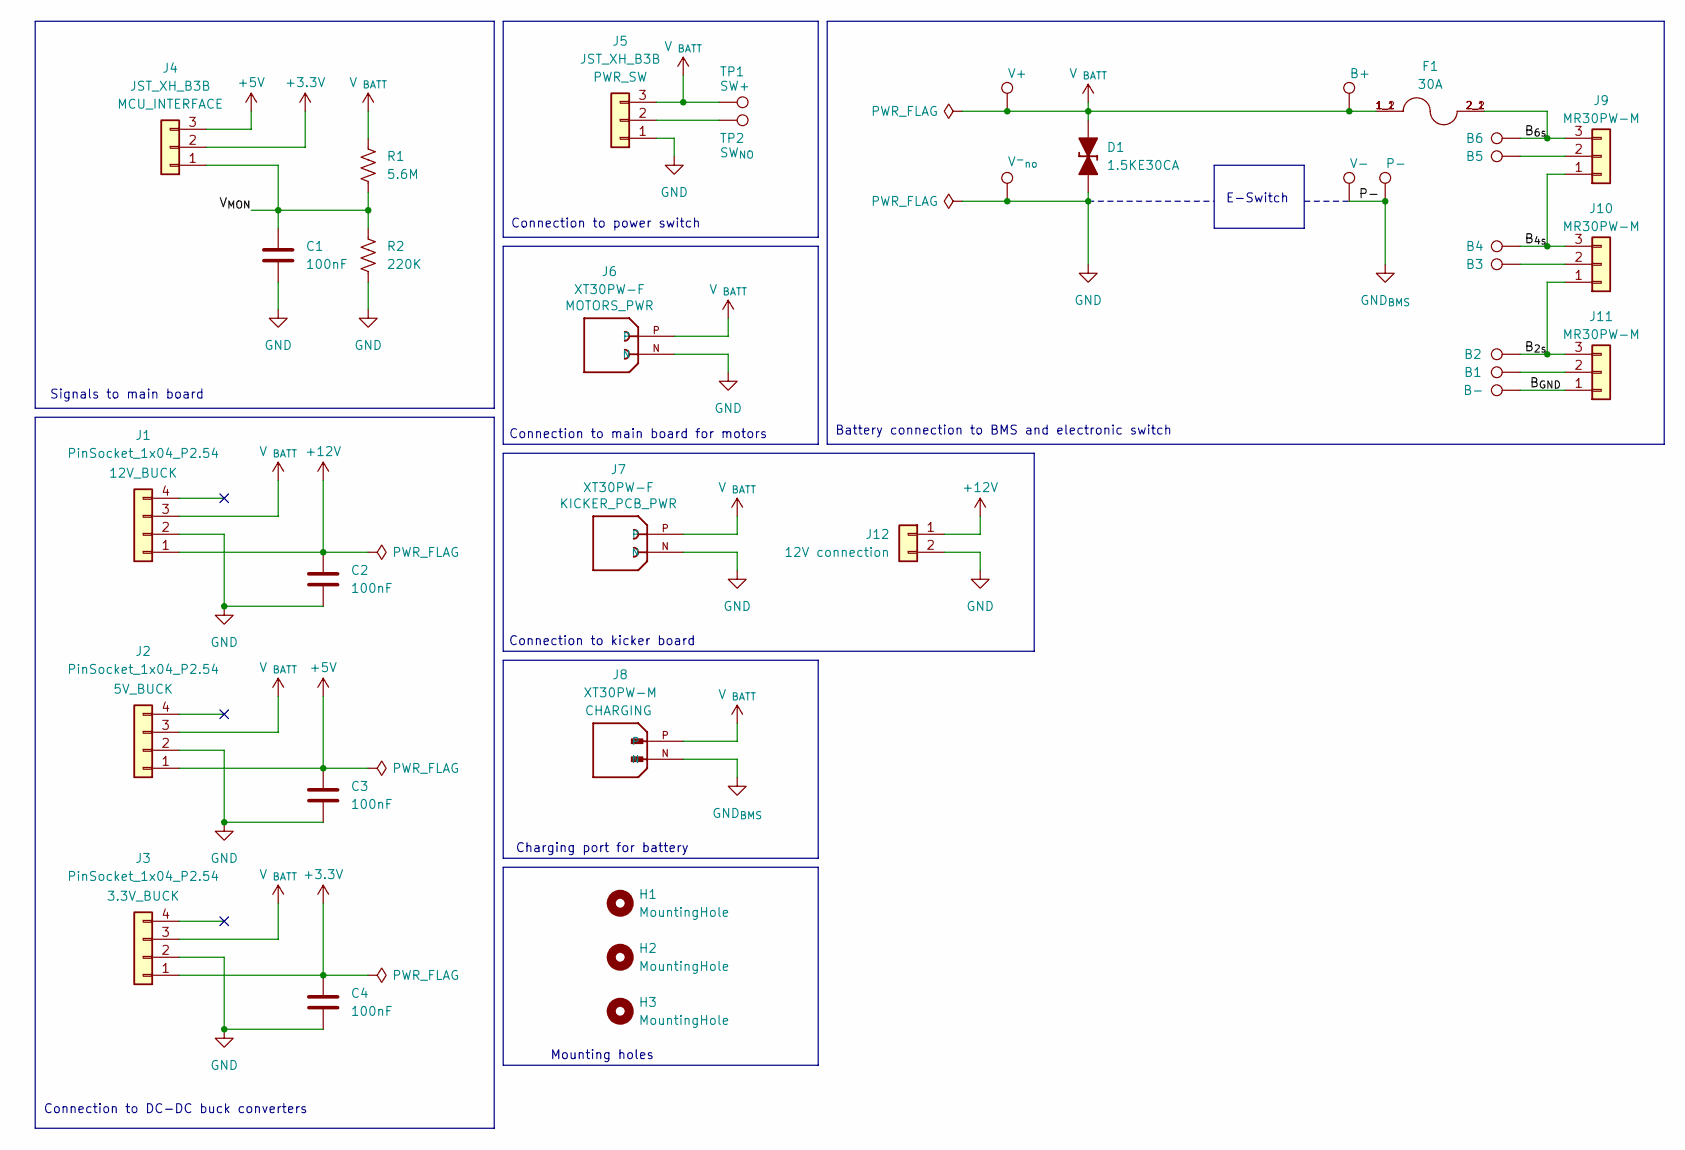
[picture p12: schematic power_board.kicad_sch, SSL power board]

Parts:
C1, C2, C3, C4: 100nF; C_Disc_D5.0mm_W2.5mm_P5.00mm
D1: 1.5KE30CA; D_DO-201_P12.70mm_Horizontal_TVS
F1: 30A; FUSE_3557-10; PARTREV D
H1, H2, H3: MountingHole; MountingHole_3.2mm_M3
J1, J2, J3: PinSocket_1x04_P2.54; PinSocket_1x04_P2.54mm_Vertical
J4, J5: JST_XH_B3B; JST_XH_B3B-XH-A_1x03_P2.50mm_Vertical
J6, J7: XT30PW-F; AMASS_XT30PW-F; PARTREV 1.2
J8: XT30PW-M; AMASS_XT30PW-M; PARTREV 1.2
J9, J10, J11: MR30PW-M; AMASS_MR30PW-M_1x03_P3.50mm_Horizontal
J12: 12V connection; JST_B2B-XH-A
R1: 5.6M; R_Axial_DIN0204_L3.6mm_D1.6mm_P5.08mm_Horizontal
R2: 220K; R_Axial_DIN0204_L3.6mm_D1.6mm_P5.08mm_Horizontal
TP1: SW+; TestPoint_Pad_D1.0mm
TP2: SW_{NO}; TestPoint_Pad_D1.0mm
TP3: V+; TestPoint_Pad_D2.5mm
TP4: V^{-}_{no}; TestPoint_Pad_D2.5mm
TP5: B+; TestPoint_Pad_D2.5mm
TP6: V-; TestPoint_Pad_D2.5mm
TP7: P-; SolderWirePad_1x01_SMD_5x10mm
TP8: B6; TestPoint_THTPad_D2.0mm_Drill1.0mm
TP9: B5; TestPoint_THTPad_D2.0mm_Drill1.0mm
TP10: B4; TestPoint_THTPad_D2.0mm_Drill1.0mm
TP11: B3; TestPoint_THTPad_D2.0mm_Drill1.0mm
TP12: B2; TestPoint_THTPad_D2.0mm_Drill1.0mm
TP13: B1; TestPoint_THTPad_D2.0mm_Drill1.0mm
TP14: B-; SolderWirePad_1x01_SMD_5x10mm

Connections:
+3.3V: C4.2, J3.1, J4.2
+5V: C3.2, J2.1, J4.3
+12V: C2.2, J1.1, J12.1
/B_{2s}: J10.1, J11.3, TP12.1
/B_{4s}: J9.1, J10.3, TP10.1
/B_{6s}: F1.2_1, F1.2_2, J9.3, TP8.1
/B_{GND}: J11.1, TP14.1
/V_{MON}: C1.2, J4.1, R1.2, R2.1
GND: C1.1, C2.1, C3.1, C4.1, D1.2 (A), J1.2, J2.2, J3.2, J5.1, J6.N, J7.N, J12.2, R2.2, TP4.1
GND_{BMS}: J8.N, TP6.1, TP7.1
unnamed: J5.2, TP2.1
unnamed: J9.2, TP9.1
unnamed: J10.2, TP11.1
unnamed: J11.2, TP13.1
V_{ BATT}: D1.1 (K), F1.1_1, F1.1_2, J1.3, J2.3, J3.3, J5.3, J6.P, J7.P, J8.P, R1.1, TP1.1, TP3.1, TP5.1

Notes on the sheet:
Connection to DC-DC buck converters
Connection to main board for motors
Charging port for battery
Signals to main board
E-Switch
Battery connection to BMS and electronic switch
Mounting holes
Connection to kicker board
Connection to power switch

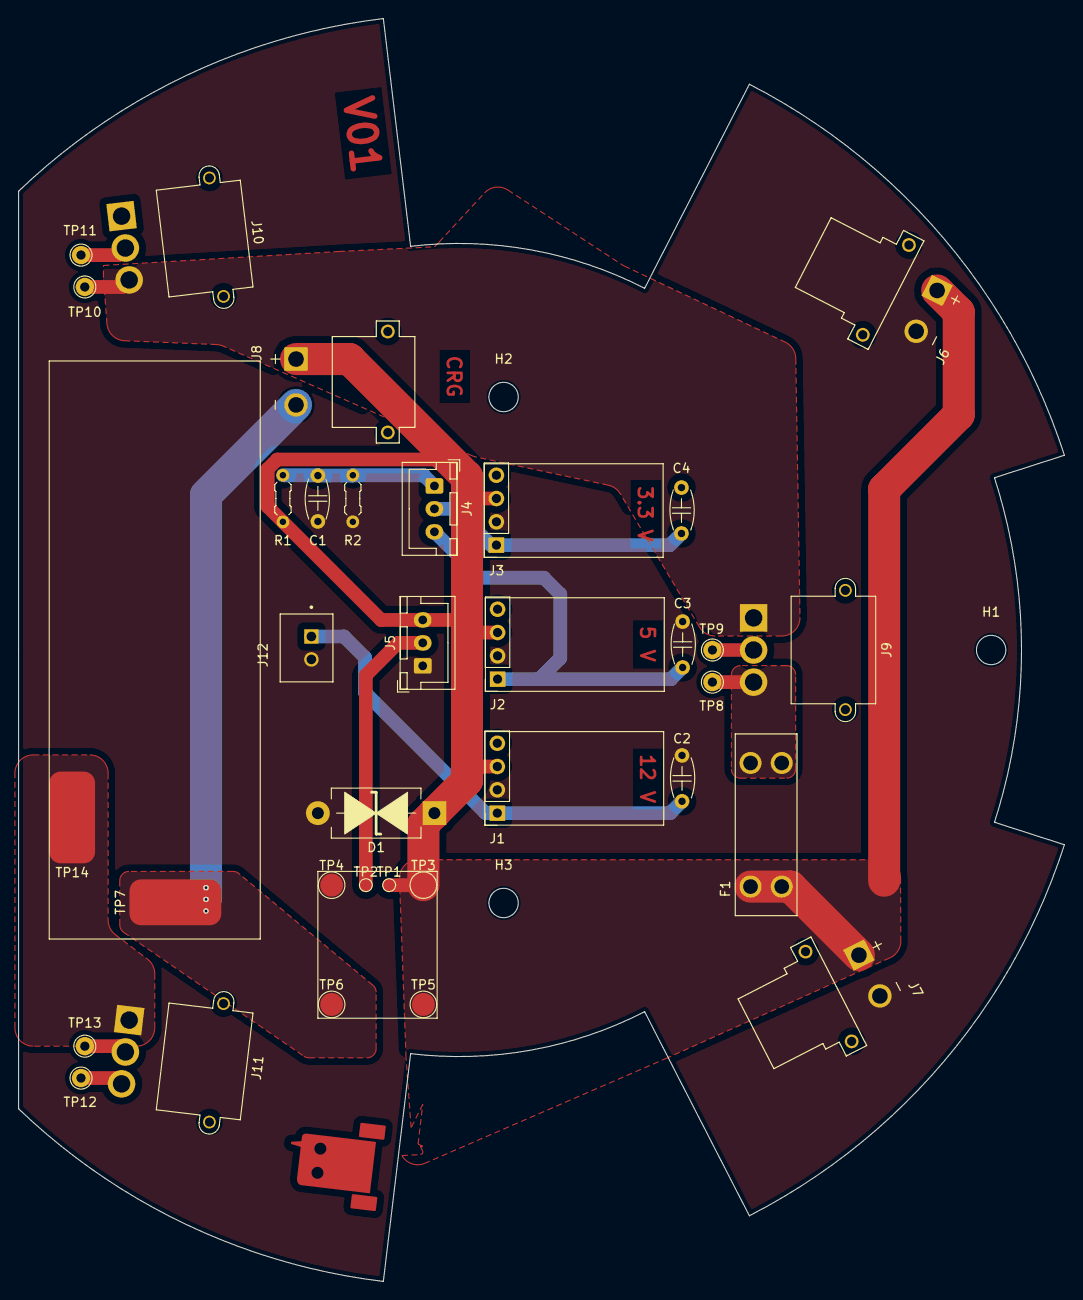
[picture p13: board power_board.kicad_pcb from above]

Board: 2 copper layers, 114.0 x 137.6 mm, 37 parts (0 on the bottom side), 15 nets.

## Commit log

2025-05-05 Add structure and files for the prototypes
    [connectors.kicad_sch, esp32.kicad_sch, main.kicad_pcb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]
2025-05-24 First version with 12x8 cm proofboard.
    [esp32.kicad_sch, main.kicad_pcb, motors.kicad_sch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]
2025-10-03 Add power board
    [power_board.kicad_pcb, power_board.kicad_sch, power_board.step]
2025-10-03 Edits for custom board
    [esp32.kicad_sch, motors.kicad_sch]
2025-10-05 Added Kicker PCB
    [Kicker_LT3751_OxeBots.kicad_pcb, Kicker_LT3751_OxeBots.kicad_sch]
2025-10-05 feat: radio and motor encoders
    [esp32.kicad_sch, main.kicad_sch, motors.kicad_sch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]
2025-10-05 feat: imu
    [esp32.kicad_sch, imu.kicad_sch, main.kicad_sch]
2025-10-06 Update for CNC
    [power_board.kicad_pcb, power_board.kicad_sch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]
2025-10-06 fea: add jumpers to I2C encoders config
    [esp32.kicad_sch, imu.kicad_sch, main.kicad_sch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]
2025-10-06 Add NRF24L01 footprints & symbols
2025-10-06 wip: change radio footprint
    [imu.kicad_sch, motors.kicad_sch, radio.kicad_sch]
2025-10-07 Created PCB for footprint tests
    [teste_footprint.kicad_pcb, teste_footprint.kicad_sch]
2025-10-07 feat: association of footprints
    [imu.kicad_sch, motors.kicad_sch, radio.kicad_sch]
2025-10-07 Add BOM & gcode for manufacturing
2025-10-08 Start layout
    [main.kicad_pcb]
2025-10-08 Fix jumpers
    [main.kicad_pcb, motors.kicad_sch, power.kicad_sch]
2025-10-08 Preliminary placing components
    [main.kicad_pcb, power.kicad_sch]
2025-10-08 Add step file
    [main.kicad_pcb]
2025-10-09 feat: roteamento do main PCB
    [main.kicad_pcb]
2025-10-09 Add manufacturing files for tester board
    [teste_footprint-F_Cu.gbr, teste_footprint-job.gbrjob, teste_footprint.drl]
2026-01-30 First commit of Kicker Board
    [Kicker_LT3751_OxeBots.kicad_pcb, Kicker_LT3751_OxeBots.kicad_sch]
2026-01-30 Updated Solenoid Circuit
    [Kicker_LT3751_OxeBots.kicad_sch]
2026-02-06 Alteração GY-85
    [main.kicad_pcb]
2026-02-08 Conserto do nome
    [main.kicad_pcb]
2026-02-08 Update repo README and main PCB title header
    [main.kicad_pcb]
2026-02-11 alteração antena
    [main.kicad_pcb]
2026-03-03 correção nrf24lo1
    [main.kicad_pcb]
2026-03-18 Updated feedback circuit
    [Kicker_LT3751_OxeBots.kicad_pcb, Kicker_LT3751_OxeBots.kicad_sch, aaa.kicad_pcb]
2026-04-24 Fix pcb
    [esp32.kicad_sch, imu.kicad_sch, main.kicad_pcb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]
2026-05-25 adding ldo regulador to radio
    [esp32.kicad_sch, imu.kicad_sch, main.kicad_pcb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]
2026-05-25 Add TOF symbol and refactor the schematic to be cleaner
    [esp32.kicad_sch, imu.kicad_sch, main.kicad_sch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]
2026-05-25 Update footprint for TOF and encoders
    [main.kicad_sch, motors.kicad_sch]
2026-06-09 Add 74HC595 shift register into the schematic
    [main.kicad_sch]
2026-06-27 update
    Placa parcialmente desenhada, componentes posicionados
    [Kicker_LT3751_OxeBots.kicad_pcb, Kicker_LT3751_OxeBots.kicad_sch, aaa.kicad_pcb]

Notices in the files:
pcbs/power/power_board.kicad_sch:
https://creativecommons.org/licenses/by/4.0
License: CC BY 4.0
